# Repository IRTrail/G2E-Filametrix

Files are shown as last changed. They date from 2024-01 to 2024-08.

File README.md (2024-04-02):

# G2E and Filametrix
## _Modifications for the G2E to have a Filametrix cutter and toolhead sensors._  
#### Thanks to sundee, jmaurin, jelliebean, gsx8829, CheeseFrog, and kinematicdigit for suggestions and feedback. Thanks to any of you who have come here and print these parts. You're what it's all about.  
#### Special thanks to JaredC01 and Sorted for their amazing designs.
I am on discord @ Silverback_Attack.  

This version is based on the released CAD from JaredC01. For any parts not included here, you'll need to go to that repository.  

I have depreciated the single and non-sensor versions since I have not heard of anyone using them. If you want them, the versions previously here and based on beta CAD are in the `Depreciated` branch of this repo. I have no plans to continue supporting the other versions.  

Also, because I want to be transparent with you my esteemed colleagues, I have an affiliate status with Amazon, and get a tiny kickback if you click and buy on the links. I'll only suggest stuff I have used and had success with though.  

#### Use at your own risk. It's not my fault your sister is ugly or your tongue hurts when you lick a 9V battery...or anything else. Just saying.  
<h1>The G2E-Filametrix "Twinsor" (Dual Sensor)</h1>

<p align="center">
	Twinsor
</p>

### _All Licenses are carried over from their respective creators. Read them here:_
https://github.com/sorted01/Filametrix  
https://github.com/JaredC01/Galileo2  
If not otherwise licensed, the files herein are covered by GPL V3. See LICENSE in this directory.  

## Ok, so what do I need to print?  
You'll need to print:  
### [KinematicDigit's calibration cube](https://www.printables.com/model/570510-swiss-cheese-calibration-cube)  

<b><ins>Print this ***FIRST!***</ins> If you can't make this work, tune your printer. Most of the issues with switch activation can be solved with a finely tuned printer. Unfortunately, there's no real good way to get around the 0.5mm activation range of the D2F switch.  

<ins>***Your prints must be on point!***</ins>   

Furthermore, if you ask me why your switches don't work correctly, I'll likely ask to see some detailed photos of this cube and the ERCF calibration print.</b>  

### [Switch test block](https://github.com/IRTrail/G2E-Filametrix/tree/main/Print%20Test%20Block)  

I have provided a switch test block. You can print one, install a ball and switch, and see how it works without printing the entire front body.  
- You should be able to pass filament through it with no perceptable drag before installing the switch.
- The ball should drop in to the cavity. No forcing it at all. Literaly just drop into place.
- The switch should fit snugly with a slight push. It should not need forced.
- The support should pop out with little trouble
- After installing the switch and ball, the ball should rattle a bit if you shake the block without filament in it.   
- The switch should activate reliably.
- If something above isn't right, go back and tune your prints. I know, you've been printing since dot matrix was a thing and the PIF guys ask you for advice on making better prints. I get it. I do. But, seriously, go back and tune your prints. Every issue, except two, has come down to print quality. So, <b><ins>go back and tune your printer.</ins></b>
- [Here's a short video](https://youtu.be/y9Mo5xBN0B0)

### After tuning your printer, print these:
 - [ ] One front of the G2E extruder body.
 - [ ] One G2E extruder rear body. This is the same between all versions.
 - [ ] One arm of either version (See below)
	- The Stylized arm works with the printheads here.
	- The "wide" arm works with the original Filametrix printheads. It also works with the printheads here, but for either, you'll need a screw in the ADXL mount hole, just like the original Filametrix setup.
 - [ ] A front and back of your desired print head.
	- The rear is often the same between versions of the same hotend. I.E. The Rapido V1 rear will work for the Standard Rapido V1 and the Rapido V1 UHF.
 - [ ] The remaining parts from the main G2E repository linked above.
 - [ ] The remaining parts from Filametrix linked above (blade holder etc.)  
## Great, what else do I need?
Well, pretty much what is in the parent repos linked above.
- The G2E extruder bodies use all the same hardware as the original and the only change was to carve out some material for the arm and switches, and modify the filament path a bit so the switches actuate more reliably. Thus, it uses the same hardware.
- The Filametrix printheads I have adapted in this repository have a socket head screw instead of a countersink screw at the pivot. Not a big deal, and if you want to modify yours for the countersink, have at it. I just have way more socket head screws laying around than countersink.
- You'll need two D2F microswitches. I've been just taking the lever off and it seems to work well. I didn't design for the lever, so if you use it, that's your choice and let me know how it goes. I bought a pack of 30 from Amazon. (Affiliate link to the [ones I bought](https://amzn.to/3wfdvVp))
- You'll need two 5.5mm ball bearings. (Affiliate link to [the ones I bought](https://amzn.to/4bB7HpA) or [these work as well](https://amzn.to/3Vf1sli))  
## Right on. But, I'm a true badass and mangled the depressor. Got anything for me?
You bet'cha. Check out the `Beefy Depressor` folder. It should mount in the same location as the standard one, but hey, you don't know your own strength, so use washers on every M3 x 10 Socket head screw. It's important. Don't be like this guy:  
<p align="center">
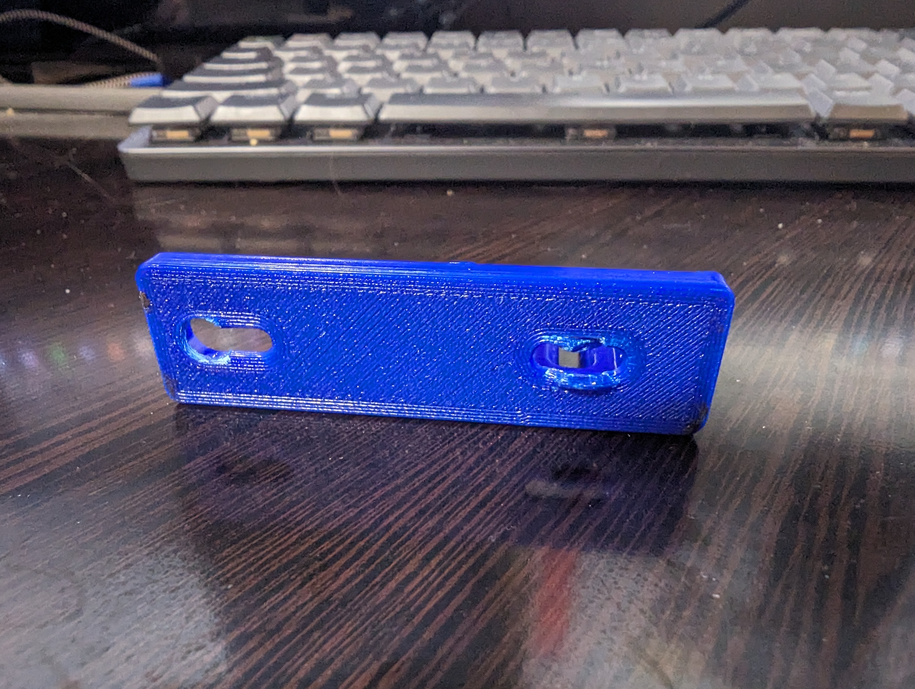
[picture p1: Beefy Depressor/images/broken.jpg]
busted depressor
	
</p>  

## The more boring stuff, but still important...kinda.
- Unless otherwise stated below, all the build notes from the G2E and Filametrix apply. If you look things over, you should get the idea.  

#### There are two arm versions.  
- One is a wide version which uses the screw in the ADXL hole for a stop.  
The other is a stylized arm which has an integral stop which does not use the screw. However, it does obscure the ADXL hole somewhat.  
- I have been told it is a PITA to install with the spring and washers and all without the screw stop. (I didn't know there were supposed to be washers!)
- The easiest way I have found is with the front and back separated. You put the screw through the pivot point, then add a washer. Then the spring goes in the arm and you simultaneously slide the arm on the screw while guiding the other end of the spring into the recess. Then place the second washer on the screw. Now you can mate the front and back parts of the printhead fairly easily.  

## Extruder and Hotend Measurements
These are taken from CAD and are just calculations for reference. I am not sure what nozzle you use, so just measure it with the stinger of your calipers and add that to these values where asked in the Happy-Hare software.
### Rapido 1:
<p align="center">
	
</p>  

#### Here's what I have for the Rapido 2 standard flow hotend with the Twinsor. I have found them to be the same as the Rapido 1 standard flow.
- Note that these are taken from Happy Hare 2.5.0.
- Yours may be located in a different config file if you don't have the same version of Happy Hare.  
- Also, understand these are what work for me. You may have different values. But, hopefully these are a good starting point for you.  

From mmu_parameters.cfg:  
mmu_parameters
From mmu_macro_vars.cfg:   
mmu_macro_vars

### Revo
<p align="center">
	
</p>  

<ins>_These are only measured from CAD and not tested._</ins>  

### Troubleshooting:
If your switches don't activate correctly:
- Go back and print the swiss cheese calibration block.
- Tune your printer using [Ellis' guide](https://ellis3dp.com/Print-Tuning-Guide/). Step through it one step at a time and DON'T SKIP ANY STEPS.
- Try a different switch. I have found that some of the Amazonium switches vary in their activation range. Chances are a different switch (even from the same box of 50 you bought) will work better. I bought [these (affilate link)](https://amzn.to/49HGtfB) and they are decent. I haven't had much issue with them, but most of the time, if a user's print is dialed in, a different switch will help.
### Input Shaper and Resonance Tuning
I have found that the balls tend to rattle around and make an extra hump in the frequency graph. So, because you've changed the mass of the toolhead and are going to redo input shaper (...right?) I would suggest just cutting off about a 15cm length of filament and pushing that throught the printhead to hold the balls steady, or just feed filament from the MMU down to the toolhead. Then run input shaper. That tends to make a more realistic graph since there will be filament in the printhead while printing.  
### A few words about the blade
I have found the #4 blades to be of poor to low quality through Amazon. [I got these](https://amzn.to/3PAReIw). The steel seems to be good, but the edge isn't honed well. I would suggest a few swipes across a sharpening stone to hone it to a keen edge.
### NOTES:  
I have included all the necessary parts in each folder...I think. Please let me know of you find something missing.  
They should be oriented to print with no issues.  
- If you don't see something, or it's oriented incorrectly, please let me know. This project kinda blew up in a hurry and I did my best.  

The necessary supports are included and should be discarded after printing.  
The standard Voron print settings should work quite well here.  
Some other print heads are available, and I am working through the others as I get requests for them. They're located in "Other Printheads".  
-- If you see something amiss in there, please let me know.

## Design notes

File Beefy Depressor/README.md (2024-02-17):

# Beefy Depressor
#### With respect to Sorted for the original design.
So, you have done countless swaps and find that the cutter is weak, seems to have no vigor, and just doesn't cut it anymore. I get it. It happens. You need a ***BEEFY*** depressor. I have your back my dude.  
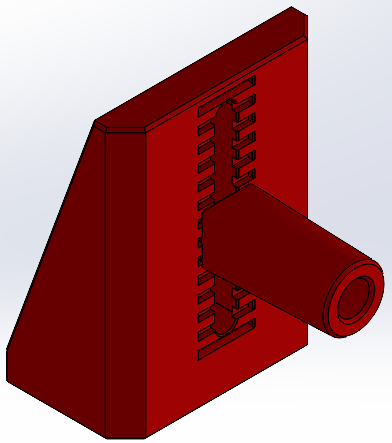
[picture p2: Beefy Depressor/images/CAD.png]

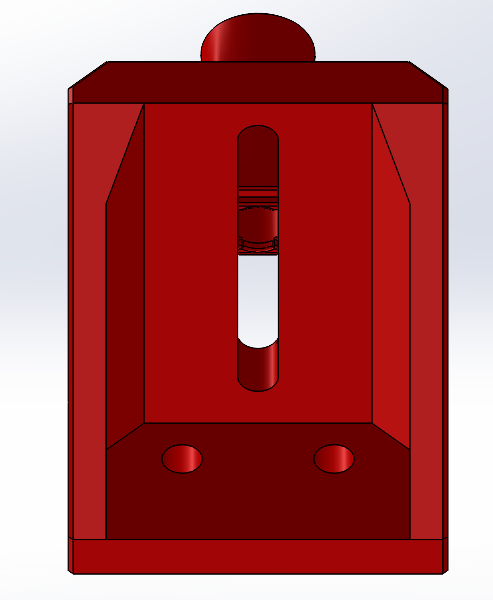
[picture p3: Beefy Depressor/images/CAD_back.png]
  
There's no counterbored or chamfered slots in this one. Just pure 100% raw Angus Waygu BEEF. Use M3 x 10 bolts in each location. Add a washer to each one to decrease chance of pull-through.

Now, you should have no more bull.  


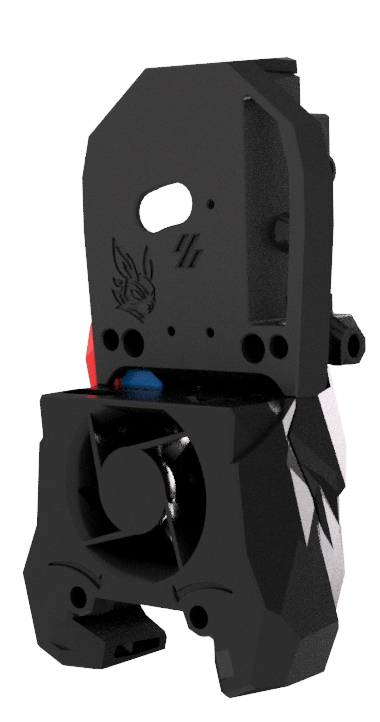
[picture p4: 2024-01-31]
images/Filametrix for G2E - Baseline.png

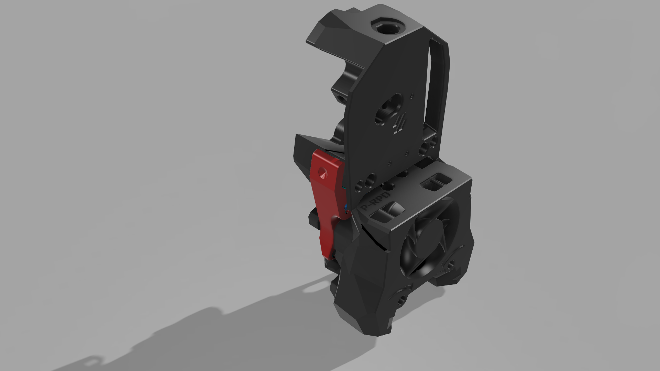
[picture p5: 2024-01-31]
images/Filametrix for G2E.png

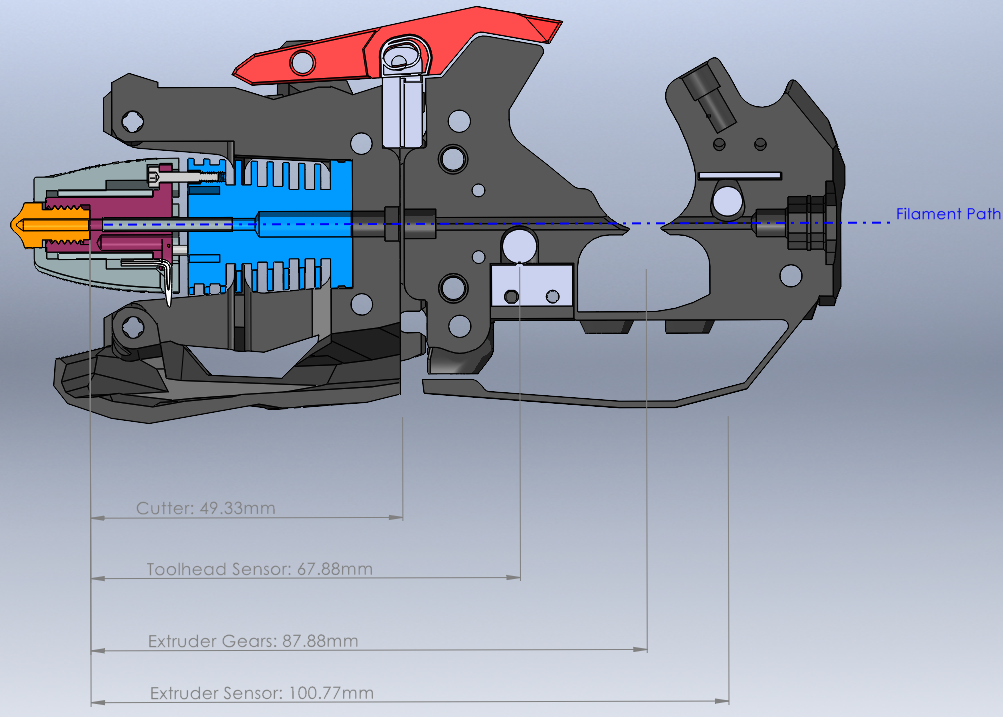
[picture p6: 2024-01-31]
images/Rapido Twinsor Lengths.png

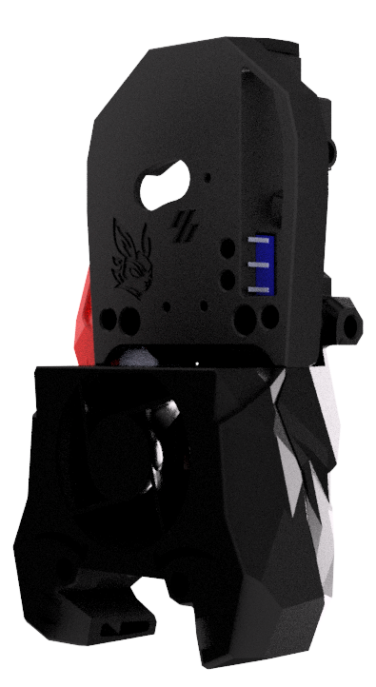
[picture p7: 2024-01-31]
images/Filametrix for G2E - Single Sensor.png

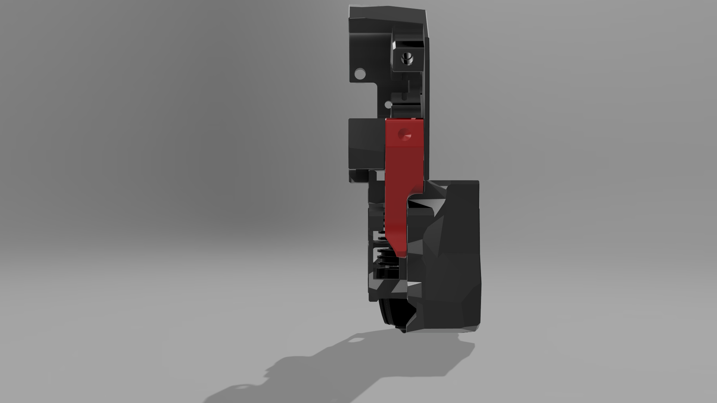
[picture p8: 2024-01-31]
images/Filametrix for G2E side view.png

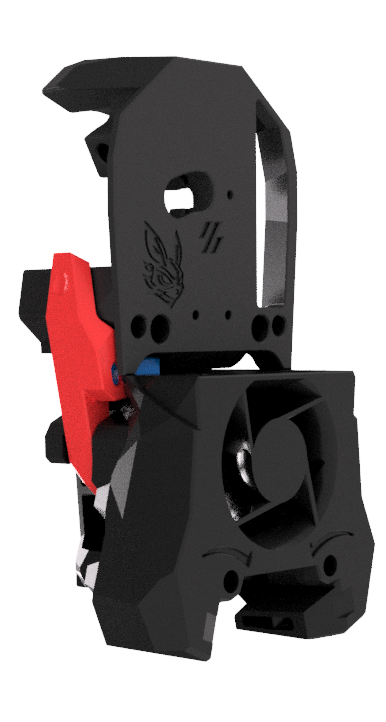
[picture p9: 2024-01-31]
images/Filametrix for G2E - Baseline_2.png

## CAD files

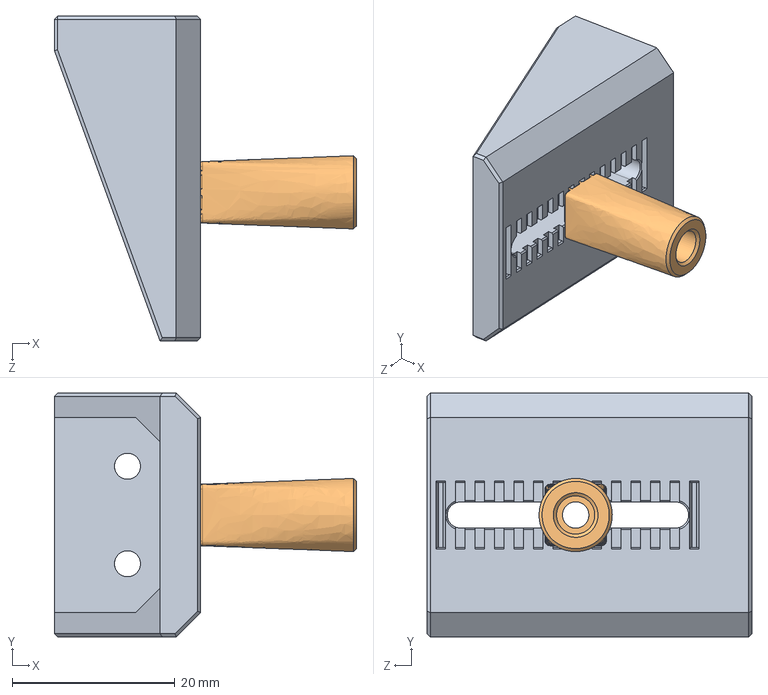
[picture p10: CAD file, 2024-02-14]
Beefy Depressor/CAD/beefy_depressor_mount_assembly.STEP
37.2 x 30.0 x 40.0 mm
depressor_mount_Part1
depressor_Part1

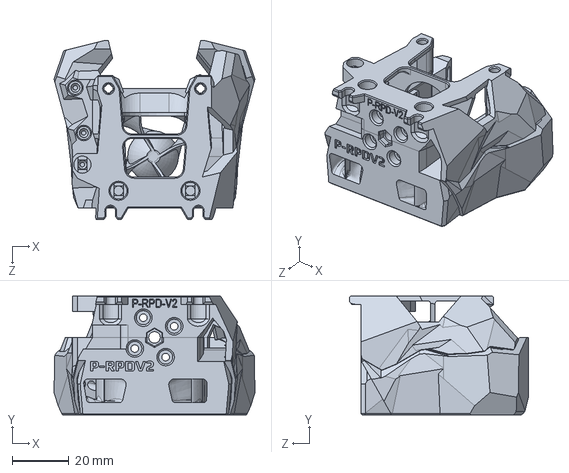
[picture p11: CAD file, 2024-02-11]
Printheads/Rapido 2/Solidworks/SB_Rapido V2_Filametrix_Assembly.SLDPRT
71.1 x 42.0 x 63.1 mm

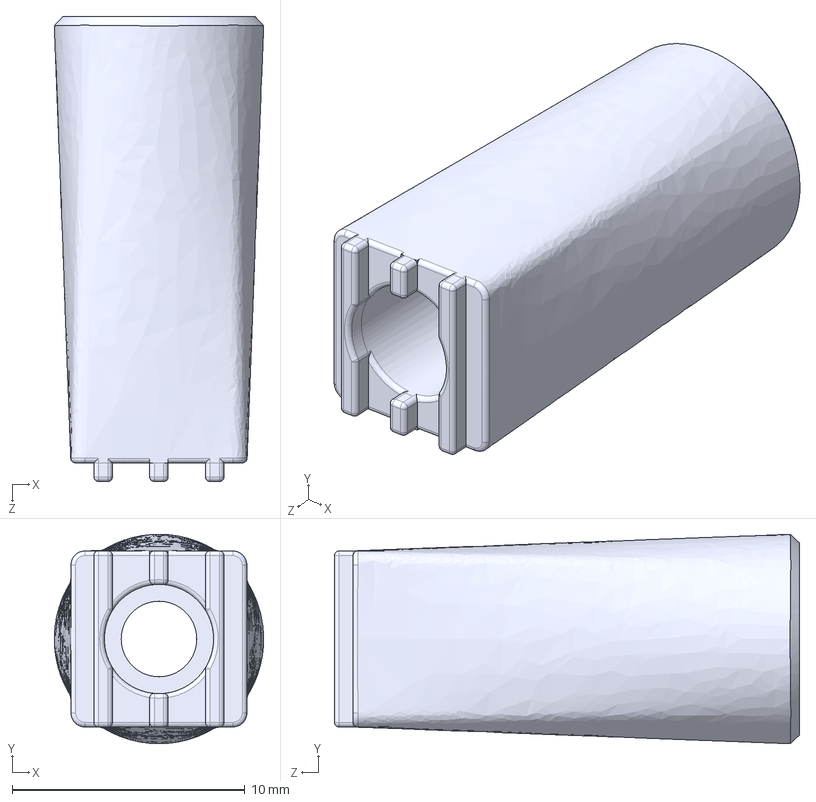
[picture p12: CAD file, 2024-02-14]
Beefy Depressor/CAD/depressor.STEP
9.01 x 9.01 x 20.0 mm

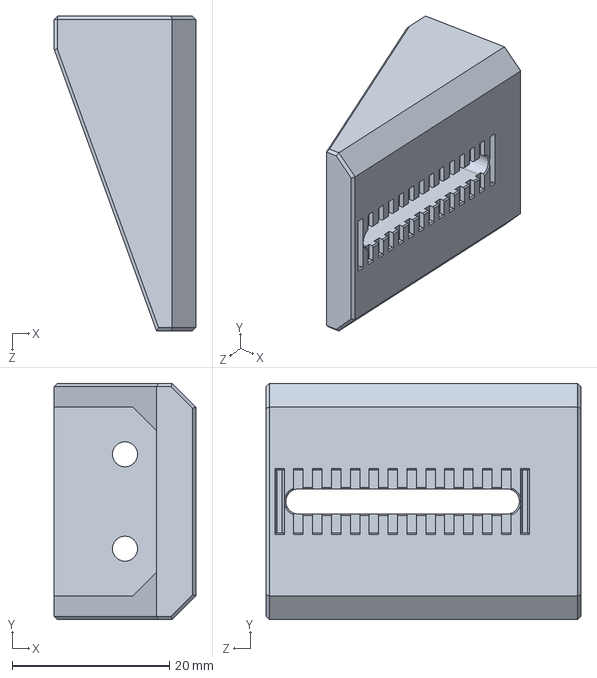
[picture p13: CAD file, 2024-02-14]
Beefy Depressor/Solidworks/depressor_mount.SLDPRT
18.0 x 30.0 x 40.0 mm

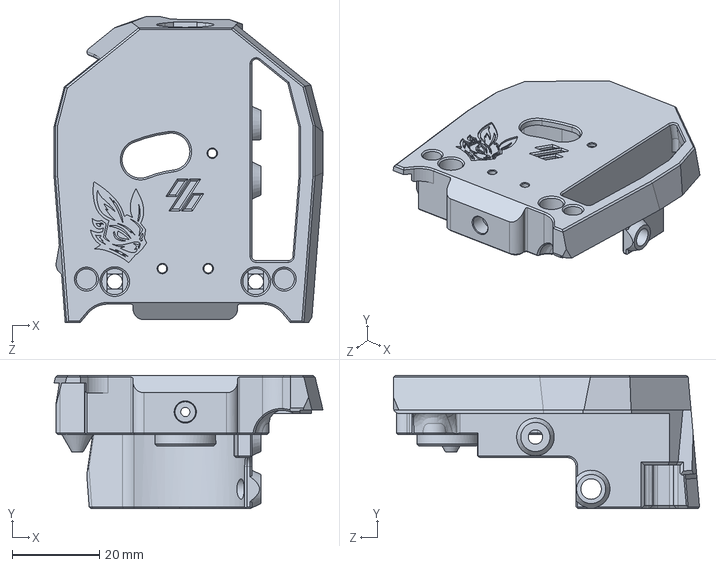
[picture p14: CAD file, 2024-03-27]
Extruder and Cutter Parts/Non-sensor/CAD/front_body_ECAS_coupler_no_sensor.STEP
61.8 x 30.6 x 70.3 mm

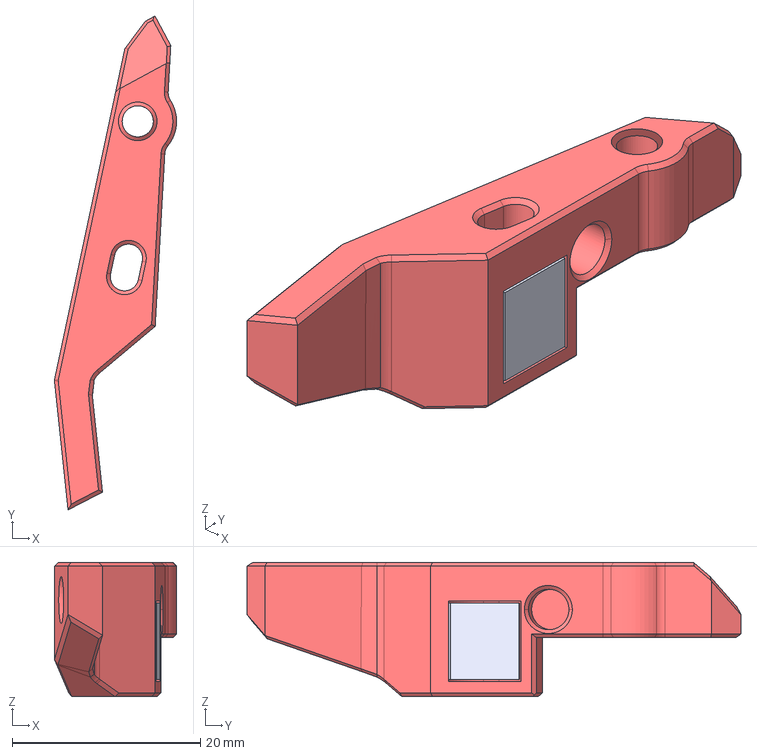
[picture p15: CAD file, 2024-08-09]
Extruder and Cutter Parts/Twinsor/CAD/arm 4 degrees.step
13.0 x 52.4 x 14.3 mm

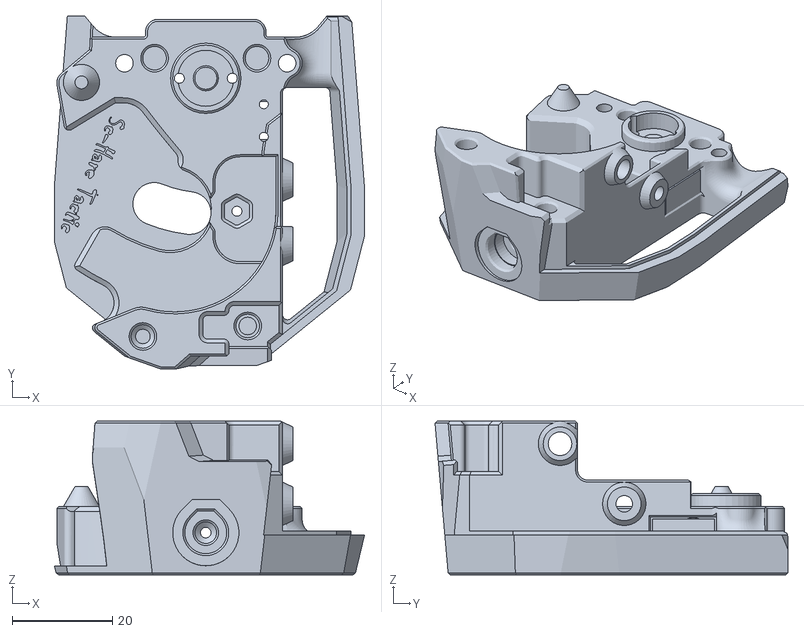
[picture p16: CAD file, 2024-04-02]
Extruder and Cutter Parts/Twinsor/STL/G2E_Filametrix_Twinsor_Front.STL
61.8 x 70.3 x 30.6

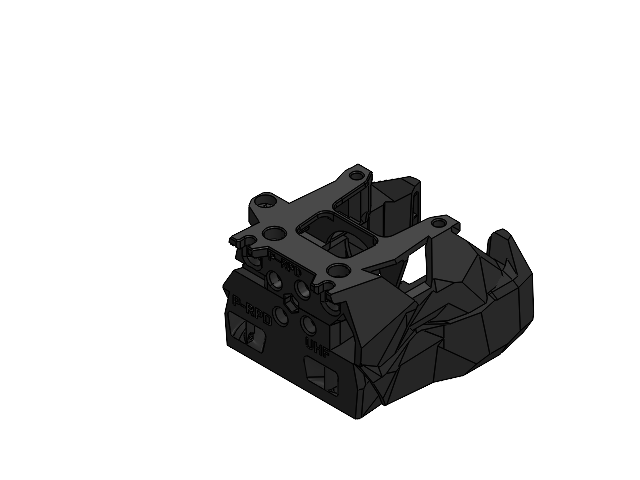
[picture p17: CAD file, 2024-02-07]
Printheads/Rapido UHF/Solidworks/SB_Rapido_UHF_Filametrix.SLDASM
SB Rapido UHF
Rapido Rear

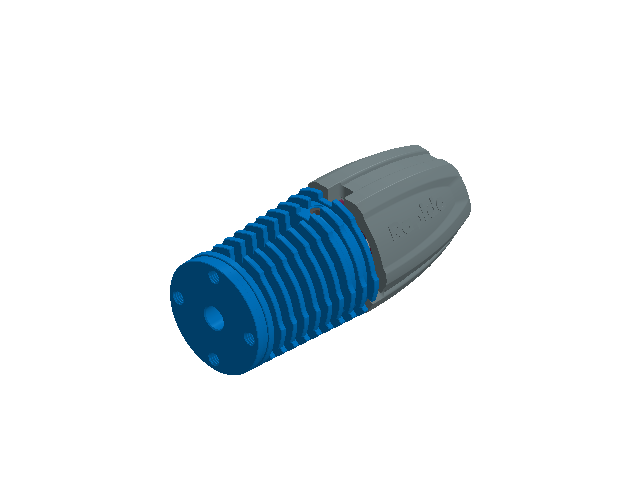
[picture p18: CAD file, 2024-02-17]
Twinsor/SOLIDWORKS/Rapido Hotend HF.SLDASM
Rapido Hotend HF1
Rapido Hotend HF3
Rapido Hotend HF4
Rapido Hotend HF5
Rapido Hotend HF6
Rapido Hotend HF7
Rapido Hotend HF8
Rapido Hotend HF9
Rapido Hotend HF10
Rapido Hotend HF11
Rapido Hotend HF12
Rapido Hotend HF14
Rapido Hotend HF15
Rapido Hotend HF16
Rapido Hotend HF17
Rapido Hotend HF18
Rapido Hotend HF19
Rapido Hotend HF21
Rapido Hotend HF22
Rapido Hotend HF23
Rapido Hotend HF25
Rapido Hotend HF26
Rapido Hotend HF28
Rapido Hotend HF29
Rapido Hotend HF30
Rapido Hotend HF31

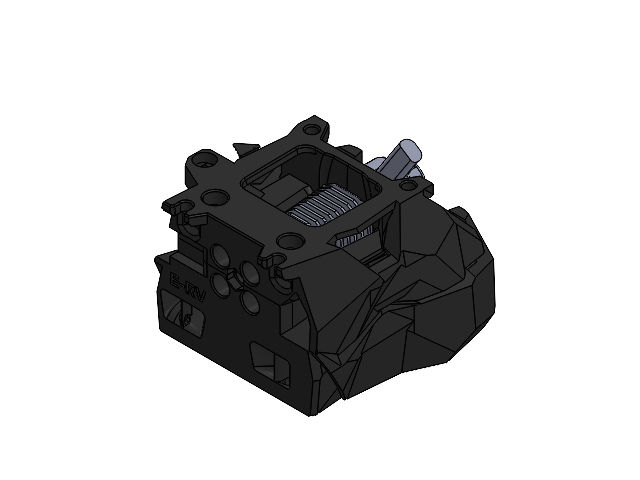
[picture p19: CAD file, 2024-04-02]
Printheads/Revo/Solidworks/G2E - Revo - Filametrix - Assembly.SLDASM
G2E - Revo - Filametrix - Front
G2E - Revo - Filametrix - Rear
revo_voron_reference_cad

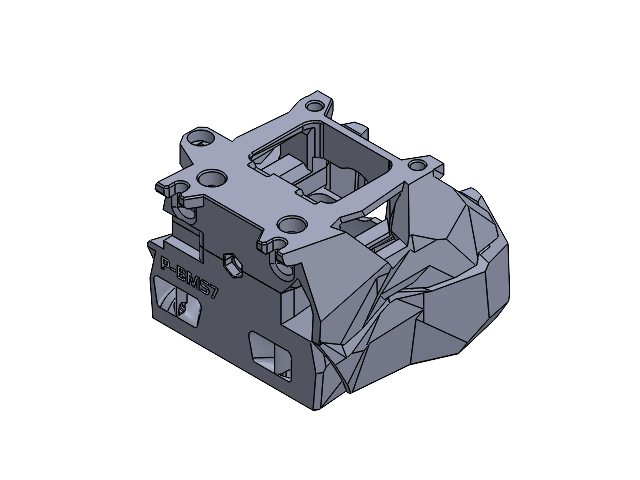
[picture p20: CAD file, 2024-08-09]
Printheads/BMS 7 Fin/Solidworks/BMS 7 Fin.SLDASM
BMS_Front
BMS_Rear_2

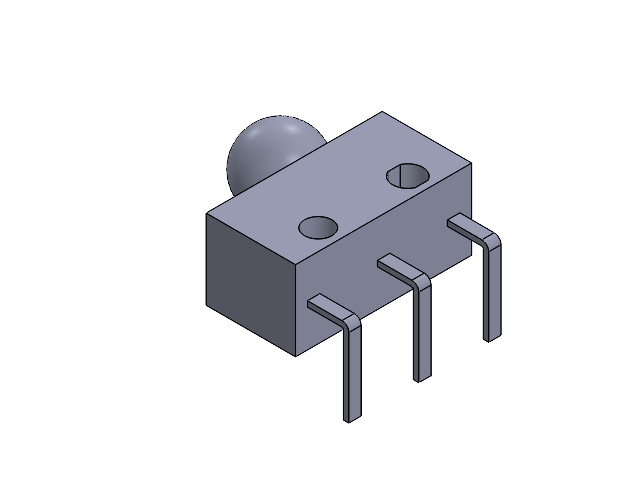
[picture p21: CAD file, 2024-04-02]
Extruder and Cutter Parts/Twinsor/SOLIDWORKS/Switch and Ball_Switch and Ball.SLDASM
5.5mm Ball_5.5mm Ball
D2F_01L_A1_BASE (1)_D2F_01L_A1_BASE (1)

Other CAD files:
Extruder and Cutter Parts/Twinsor/SOLIDWORKS/Switch and Ball (1)_Switch and Ball (1).SLDASM
Extruder and Cutter Parts/Twinsor/SOLIDWORKS/Twinsor Front Body and Switches_Twinsor Front Body and Switches.SLDASM
Extruder and Cutter Parts/Twinsor/SOLIDWORKS/Rapido Assembly.SLDASM
Extruder and Cutter Parts/Twinsor/SOLIDWORKS/Stealthburner_Printhead_Rapido_V2.SLDASM
Beefy Depressor/STL/better_depressor_mount.STL
Extruder and Cutter Parts/Twinsor/SOLIDWORKS/Blade Holder.SLDPRT
Beefy Depressor/CAD/beefy_depressor_mount.STEP
Beefy Depressor/STL/depressor-RE.STL
Beefy Depressor/STL/depressor.STL
Beefy Depressor/Solidworks/Beefy Depressor Mount.SLDASM
Beefy Depressor/Solidworks/depressor.SLDPRT
Extruder and Cutter Parts/Non-sensor/STL/front_body_ECAS_coupler_no_sensor.STL
Extruder and Cutter Parts/Twinsor/CAD/rear_body.STEP
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

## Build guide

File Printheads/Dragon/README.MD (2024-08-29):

# For Dragon HF
Please see the following printables page:
  https://www.printables.com/model/990001-dragon-hf-filametrix-mount

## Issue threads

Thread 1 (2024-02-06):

Dragon Hotend support

nzzane, 2024-02-06:
Hi there,

Love the work you have done with this, just wondering if you could make a version top support the Dragon hotend?

IRTrail, 2024-02-07:
Look in "Other Printheads" -> "Dragon"

Let me know if it has any issues.

Thanks.

Closed 2024-02-07.

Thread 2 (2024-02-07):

bug: Rapido UHF Front not modified for m3 nut

bdistin, 2024-02-07:
The front section of the Rapido UHF file has a rounded entrance for the filament rather than hex needed for the m3 nut.

IRTrail, 2024-02-07:
Ok, thanks for the heads up. I'll get that fixed as soon as possible.

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

IRTrail, 2024-02-07:
Give it a try now. Should be fixed.

Thanks again.

Closed 2024-02-07.

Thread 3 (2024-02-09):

Rapido 2 UHF Front also not modified for the M3 nut

Brownbear1984, 2024-02-09:
Just printed out the parts for the rapido 2 UHF and while the rear has the cutout for the M3 nut the front doesn't.

IRTrail, 2024-02-09:
Sure enough. Thanks for letting me know. It should be fixed now.

Closed 2024-02-09.

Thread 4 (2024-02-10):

Parts list?

arnoldstrife, 2024-02-10:
Hi, is there a parts list? It seems the filament detection is Ball and Microswitch, but I'm not sure of what size ball bearing or Microswitch should be used. Or if there are any other parts needed? The original Filametrix didn't have a sensor, and I'm assuming most of the screws remain the same in G2E but with the additional lever screws in Filametrix, but additional documentation for that would be great.

IRTrail, 2024-02-10:
Updated readme to include switch types and ball bearing diameters. Hope it helps you out.

Closed 2024-02-10.

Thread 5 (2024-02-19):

Revo Voron Hotend request

discreteaudio, 2024-02-19:
Would love to build your design to go with my ERCF v2.  Unfortunately, I don't see the Revo Voron as an option.  Any chance to add it to the mix?  I don't see the "Other Printhead" folder you mention either.

IRTrail, 2024-02-19:
Check it ooooouuuuut!

https://github.com/IRTrail/G2E-Filametrix/tree/main/Printheads/Revo

Let me know if there are any issues with it. I just revised the CAD and haven't printed one myself.

discreteaudio, 2024-02-19:
I'll give it a go as soon as my current print finishes up!  Looking forward to the build for sure!  Thanks for the rapid response!

discreteaudio, 2024-02-21:
Got it printed last night.  Hoping to put it together this weekend after a trip to the hardware store for misc hardware.  I will keep you posted on progress.  So far everything looks fantastic.

discreteaudio, 2024-02-27:
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

I had to file out material to allow the arm to have enough travel to cut filament and retract easily.  If you edit the design, take out the black bit.

IRTrail, 2024-02-28:
Thanks for the pictures. I added a recess to help with that. I just pushed it, so give that a try to see what you think.

discreteaudio, 2024-02-29:
That did the trick!  Now to finish building everything.  LoL
Thanks again!

Closed 2024-02-19.

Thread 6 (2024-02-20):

Bottom D2F microswitch already pressed once screwed in to twinsor front

Brownbear1984, 2024-02-20:
Firstly I want to say I appreciate all the work you've done here. I'm hoping the below will make sense.

I've printed out the G2E_Filametrix_Twinsor_Front.STL 2 or 3 times now at different flow settings incase I was over or under extruding. Every time I test the fitment of the D2F and bearing in the bottom I can never actuate the switch when passing filament through. If I take the screws out and just hold the microswitch in place I can hear the "click" from the switch when passing filament through. It also looks like the holes are slightly off when I can reliably actuate the switch. The top one works fine on all the versions I've printed but the bottom may need either the bottom screws to move out slightly or the bearing to move in slightly for reliable actuation of the switch.

For reference these are the microswitches I have. https://a.aliexpress.com/_EHaO0pT

IRTrail, 2024-02-20:
Most of the issues I hear about with switches not working is a stack up of tolerances.
The data sheet on the Omron is pretty specific with only 0.5mm "pretravel" (from initial contact until switch engagement) and 0.25mm "overtravel" (how much the plunger can move after switching). I have measured different actuation distances on a few different switches, even in the same brand. I don't have genuine Omron, so they might have better manufacturing tolerances than budget brands.
I have had people report back that different switches (even from the same package) work and others have indicated that different screws have helped.
I suspect a switch with a quarter millimeter off on actuation distance along with holes that are a quarter millimeter out of diameter and possibly out of position along with screws that have threads stamped on an old die likely cause this issue for some.
Also, the ball should be 5.5mm. Those usually have pretty good tolerance, but the difference between a 5.5mm and a 5.0mm can be missed pretty easily especially if you bought an assortment like I did. This has been the cause of confusion as well. Double check with a caliper. I have tried, but my Mk I Eyeball measurement tool just doesn't work in this situation.

My advice is to try a few different switches just to see if one mates up better. I recently added a link to the switches I bought from Amazon (in the readme) and have had decent luck with them, only a couple have been out of tolerance enough to be relegated to endstop switches.

There was a fairly extensive series of tests to find the optimal distance with several different variables. The unfortunate truth is that it's really difficult to hold a quarter millimeter tolerance with a 3D printer.

Brownbear1984, 2024-02-20:
I've ordered some new switches they should arrive tomorrow so will report back once I've tested again

Closed 2024-03-01.

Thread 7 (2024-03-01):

Rapido2 toolhead missing cut off

neriux912, 2024-03-01:
Toolhead for rapido 2 missing small cutoff in corner, arm can't be pushed all the way in

IRTrail, 2024-03-01:
Try it now.

Closed 2024-03-01.

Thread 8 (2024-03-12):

bottom microswitch cant work

jerem1973, 2024-03-12:
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
the rolling ball does not go far enough into the filament passage.
result the ball presses on the microswitch without filament engaged
apart from the detail very nice work

IRTrail, 2024-03-12:
99% of these types of issues come down to print quality. The switches have half a millimeter range of actuation, which is very difficult to attain on a 3D printer. Thus, the print quality must be very good to attain reliable operation.

During the creation of this model, there was special attention paid to ensuring both switch cavities were the same distance from the centerline of the filament path. Given that only the lower switch is causing you issues and the upper is working well, I am inclined to think the issue is print quality in this case as well.

I would suggest re-reading the directions, paying special attention to the part where it says to print KinematiDigit's calibration cube first. You can use the Ellis print guide to help you tune your printer such that the calibration cube passes all the tests.

Closed 2024-03-12.

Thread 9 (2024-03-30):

Rapido 2 UHF Printhead Front

ngagnej, 2024-03-30:
Just printed the new Rapido 2 UHF printhead front, the arm for the blade doesn't clear it; It's missing the notch.

IRTrail, 2024-03-30:
Give it a shot now. Added the notch. It's a good notch. One might say its a buenos notches. XD

Closed 2024-03-30.

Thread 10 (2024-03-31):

Add a small hole to poke the ball bearing out

igiannakas, 2024-03-31:
Unfortunately my Amazon sourced ball bearings were ever so slightly larger than 5.5 mm causing them to nearly fit in the holes. However I now cannot get them out in order to ream the hole a little bit for the ball bearings to fit comfortably.

May I add a suggestion to add a 2mm hole opposite from the ball bearings as an aid to remove them? Pushing them out using some spare filament or a small tool bit.

IRTrail, 2024-03-31:
Ever so slightly as in 5.505mm or 6.005mm? The bore is 6mm and the balls should be a literal drop in fit. They should sound like a baby rattle after the switch is installed and you shake the part.

Closed 2024-03-31.

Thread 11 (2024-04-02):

Bambu Hotend Support

barrenechea, 2024-04-02:
Hi! Could support for the Bambu Hotend be added? It would be greatly appreciated!
And thanks in advance for this fantastic repo!!

IRTrail, 2024-04-02:
You might try this:
https://github.com/sorted01/Filametrix/tree/main/STL/Bambu%20Toolhead

I haven't worked on the Bambu yet, but the only difference would be the small pad which acts as a stop for the stylized arm. If it works, cool. If not, try the "Wide Arm" here:
https://github.com/IRTrail/G2E-Filametrix/blob/main/Extruder%20and%20Cutter%20Parts/Twinsor/STL/G2E_Filametrix_Wide%20Arm%20ADXL%20stop.STL

That one uses the top ADXL screw just like the original Filametrix.

I'll try to get this ported when I have some time, but hopefully the above will work in the interim.

alfadex, 2024-08-20:
Hi , for hotend e3d v6, can i use this also ?
https://github.com/sorted01/Filametrix/tree/main/STL/V6%20R6

IRTrail, 2024-08-20:
> Hi , for hotend e3d v6, can i use this also ? https://github.com/sorted01/Filametrix/tree/main/STL/V6%20R6

Yes, that will most likely work. You might need the "wide arm" linked above.

Closed 2024-08-20.

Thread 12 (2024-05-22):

Cutting arm travel is limited

WegnerDan, 2024-05-22:
I have a hard time describing this, so I made some videos:

Without the G2E on top, the travel of the cutting arm is fine:

https://github.com/IRTrail/G2E-Filametrix/assets/6908247/3e7bb79e-3903-4199-9b67-89a52a9f2ef2

When the hotend is installed to the toolhead mount, G2E limits the travel of the cutting arm more than it needs to.

https://github.com/IRTrail/G2E-Filametrix/assets/6908247/6f8d3ab7-c530-49bf-a3ca-5c4a46384f43

I think it makes sense to either extend the top of the cutting arm outward a couple mm (1)
or allow the cutting arm to travel outward a little more (2).

This would make cutting the blade to the correct length a little easier.
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

What do you think?

WegnerDan, 2024-05-22:
Some more information:

The blade in the video was shortened to 25.3 mm, because it was interfering with the filament.

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

This is a blade cut to 26 mm:
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

As a test, I've filed down the area marked with 2 in the screenshot above and the filament now clears the 26mm blade

IRTrail, 2024-05-23:
When I made this, I matched the angular deflection of the original version by Sorted. The gap in the space between the arm and the G2E bodies is about half a milimeter, iirc (been a monute).

The stop is set to match deflection as well.

There's also the "wide arm" which retains the original hook that stops against the ADXL screw if you like. It's fully interchangeable.

You're the first to mention this issue. I'll keep an eye out for more reports.

Closed 2024-05-23.

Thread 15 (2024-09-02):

Bottom switch screw thickness causing extruder to slip

subnebula, 2024-09-02:
Hey there,

First off, nice work on this! It's a really great mod and is exactly what I needed, thanks for taking the time to make it.

I just wanted to provide feedback on a very small issue I encountered with one of the screws for the bottom switch in the G2E twinsor version. Basically, I had been using an M2x10 screw that was too wide at the tip (just a straight screw, not self tapping) and it was getting in the way of the motor body's movement. This caused the filament to not be gripped enough and the extruder gear to slip on the filament. Swapping it out to a self tapping (pointy ended) M2x10 seems to have fixed the issue as it is narrow enough at the tip to allow the motor body to move a bit more.

This is probably mostly user error on my part for using the wrong screw. I thought it may be worth adding a note to the readme specifying the screw type jut in case anyone else encounters the same issue.

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

Closed 2024-12-12.

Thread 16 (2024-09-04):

E3D Revo Hotend V6

alfadex, 2024-09-04:
Youu have done great work epsecial with micro switches. I have E3D Revo Hotend V6 , is there any stl for this? I print by mistake revo but not suitable

Closed 2024-12-12.

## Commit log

2024-01-31 Moved from Voron Stuff
    [5.5mm Ball (1).SLDPRT, 5.5mm Ball and Switch(1)_5.5mm Ball_Switch and Magnet_Switch and Magnet (1)_5.5mm Ball_Switch and Magnet_Switch and Magnet (1).SLDPRT, 5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]
2024-02-02 Fixed Rapido 2 UHF files
    [SB Rapido 2 UHF Front.3MF, SB Rapido 2 UHF Front.STL]
2024-02-05 Saved with all references
    [5.5mm Ball (1).SLDPRT, 5.5mm Ball.SLDPRT, Blade Holder.SLDPRT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]
2024-02-07 Solidworks update
    [front_body_ecas_coupler.SLDPRT, rear_body.SLDPRT]
2024-02-07 Update Rapido UHF for missing hex nut cavity
    [Rapido Rear.SLDPRT, Rapido Rear.stl, Rapido Rear_Rapido Rear.STEP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]
2024-02-07 Added SB - Dragon - Filametrix
    [5.5mm Ball (1).SLDPRT, 5.5mm Ball.SLDPRT, Blade Holder.SLDPRT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]
2024-02-07 Much Updates
    [5.5mm Ball (1).SLDPRT, 5.5mm Ball (1)_5.5mm Ball (1).SLDPRT, 5.5mm Ball.SLDPRT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]
2024-02-09 Update Rapido 2 UHF front for nut recess
    [SB - Rapido V2 UHF - Filametrix - Front.3MF, SB - Rapido V2 UHF - Filametrix - Front.STL]
2024-02-11 Update files with missing blade cavities
    [SB - Rapido V2 UHF - Filametrix - Front.3MF, SB - Rapido V2 UHF - Filametrix - Front.STL, SBRapidoV2 TH Front.SLDPRT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]
2024-02-11 Update missing files
    [Blade Holder.3MF, Blade Holder.stl, Filametrix Arm for G2E.3MF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]
2024-02-11 Update files to include support bodies
    [Front Body_Front Body.SLDPRT, G2E_Filametrix_Arm.3MF, G2E_Filametrix_Arm.stl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]
2024-02-14 Add Beefy Depressor Mount
    [Beefy Depressor Mount.SLDASM, beefy_depressor_mount.STEP, beefy_depressor_mount_aaasembly.STEP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]
2024-02-14 Beefy Depressor CAD pics
2024-02-17 Fix Rapido UHF
    [5.5mm Ball (1)_5.5mm Ball (1).SLDPRT, 5.5mm Ball_5.5mm Ball.SLDPRT, Blade Holder.SLDPRT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]
2024-02-17 Fixed spring hole in Rapido 2 rear
    [G2E_SB_Rapido 2 UHF_Filametrix_Front.3MF, G2E_SB_Rapido 2 UHF_Filametrix_Front.STL, G2E_SB_Rapido 2_Filametrix_Front.STL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]
2024-02-19 Add Revo
    [G2E - Revo - Filametrix - Rear.stl, G2E -Revo - Filametrix - Rear.3mf]
2024-02-20 corrected file name
    [beefy_depressor_mount_assembly.STEP]
2024-02-28 Update Revo Printhead
    Added recess for cutting arm in front printhead part
2024-03-01 Update Rapido 2 Printhead
    [G2E_SB_Rapido 2_Filametrix_Front.3MF, G2E_SB_Rapido 2_Filametrix_Front.STL]
2024-03-05 Add support to Revo Printhead rear
    [G2E - Revo - Filametrix - Assembly.SLDASM, G2E - Revo - Filametrix - Front.SLDPRT, G2E - Revo - Filametrix - Front.stl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]
2024-03-21 Updated Revo Printhead with better support
    [5.5mm Ball (1)_5.5mm Ball (1).SLDPRT, 5.5mm Ball_5.5mm Ball.SLDPRT, Blade Holder.SLDPRT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]
2024-03-25 Update stylized arm for better pivot strength
    [Filametrix Arm for G2E.SLDPRT, G2E_Filametrix_Arm.3MF, G2E_Filametrix_Arm.stl]
2024-03-25 Updates to cad
    [5.5mm Ball (1)_5.5mm Ball (1).SLDPRT, 5.5mm Ball_5.5mm Ball.SLDPRT, Blade Holder.SLDPRT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]
2024-03-25 Prepping for released G2E update
    [5.5mm Ball and Switch(1)_5.5mm Ball_Switch and Magnet_Switch and Magnet (1)_5.5mm Ball_Switch and Magnet_Switch and Magnet (1).SLDPRT, Blade Holder.SLDPRT, Bla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]
2024-03-25 Update files to agree with released CAD
    This version is based on the released CAD from JaredC01
    [5.5mm Ball (1)_5.5mm Ball (1).SLDPRT, 5.5mm Ball_5.5mm Ball.SLDPRT, Blade Holder.SLDPRT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]
2024-03-25 Update folder name
    [5.5mm Ball (1)_5.5mm Ball (1).SLDPRT, 5.5mm Ball_5.5mm Ball.SLDPRT, Blade Holder.SLDPRT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]
2024-03-27 Added Non Sensor Version
    [5.5mm Ball (1)_5.5mm Ball (1).SLDPRT, 5.5mm Ball_5.5mm Ball.SLDPRT, Blade Holder.SLDPRT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]
2024-03-30 Fix Rapido 2 UHF
    [G2E_SB_Rapido 2 UHF_Filametrix_Front.3MF, G2E_SB_Rapido 2 UHF_Filametrix_Front.STL]
2024-03-31 Add test block
    [Print Test Block.STEP, Print Test Block.STL]
2024-03-31 Small tweaks to CAD
    [5.5mm Ball (1)_5.5mm Ball (1).SLDPRT, 5.5mm Ball_5.5mm Ball.SLDPRT, Blade Holder.SLDPRT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]
2024-04-02 Update upper support
    [5.5mm Ball (1)_5.5mm Ball (1).SLDPRT, 5.5mm Ball_5.5mm Ball.SLDPRT, Blade Holder.SLDPRT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]
2024-06-02 added 4° version of cutting arm (issue 12)
    [arm 4 degrees.step, arm 4 degrees.stl]
2024-08-09 Upload BNS 7 Fin Printhead
    [BMS 7 Fin.SLDASM, BMS_7_Fin_Front.STL, BMS_7_Fin_Rear.STEP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]
